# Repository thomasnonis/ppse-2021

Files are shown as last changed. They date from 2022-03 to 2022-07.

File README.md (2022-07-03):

# Abstract
This is the repository for SALMO, the Solar Azimuth and eLevation Motorized lOcator. It is a PCB used for driving a tracking solar panel system, using GPS location and a MPPT algorithm to maximise the incident power.  
The official name of the project is `PPS2021_SUN_TRK`

# About the project
During the second semester of the 2021/2022 A.Y. of their bachelor degree in Electronics Engineering, a group of students known as _SALMO SOCIETY_, developed a custom board to solve real world problems. 
<br>Nowadays, we are all aware about climate change and it's impact, so the _SALMO SOCIETY_ decided in partecipate to the renewable energy run, in particular exploiting the energy obtained by a solar panel to drive a load.
<br>The aim of the board it's to move the solar panel using two step motors (along z-y axis) facilitating the MPP (Maximum Power Point) reaching and, as consequence, delivering the maximum power to the load.<br> Using a GPS module, the board knows exactly where it is located around the globe; afterwards the position of the sun is computed with a specific algorithm based on astronomical calculations. Then, the spatial position of the panel is derived by the accelerometer and compass modules; lastly, the motor is moved in order to follow the exact position of the sun (given its azimuth and elevation).

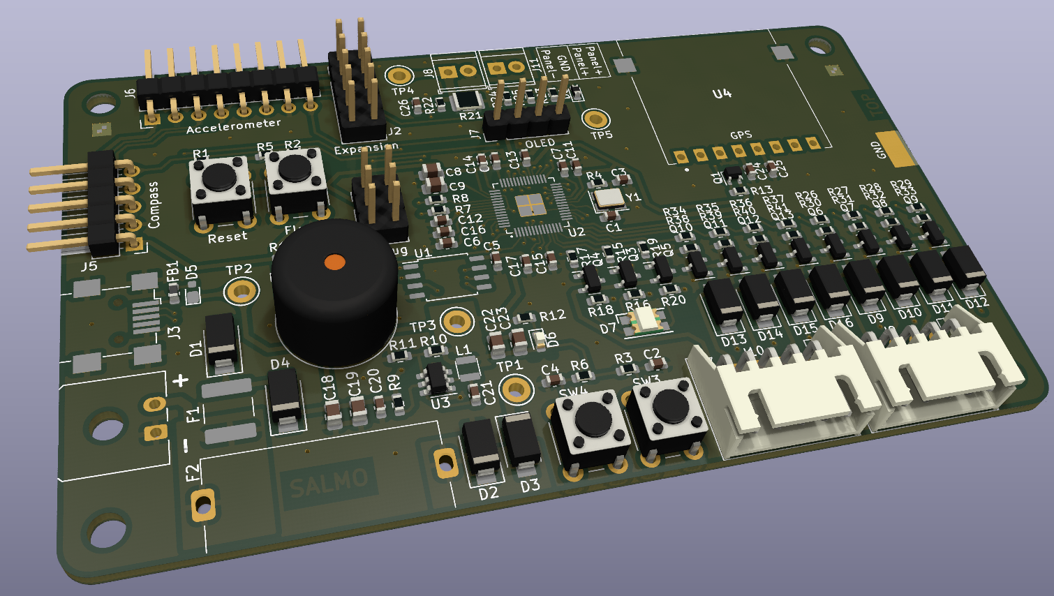
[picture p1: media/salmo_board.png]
Salmo board


# Repo structure

    📂 SALMO_pico_fw    -> Firmware 
    📂 datasheets       -> Datasheet of every component mounted on board
    📂 kicad-project    -> KiCad and gerber files 
    
# :rainbow: Building process

Debian:

    sudo apt install cmake gcc-arm-none-eabi libnewlib-arm-none-eabi build-essential

Fedora:

    sudo dnf install cmake
    sudo dnf group install "C Development Tools and Libraries" "Development Tools"
    sudo dnf install gcc-arm-linux-gnu \
    arm-none-eabi-gcc-cs-c++ \
    arm-none-eabi-gcc-cs \
    arm-none-eabi-binutils \
    arm-none-eabi-newlib

then:

    git pull
    git submodule update --init --recursive

now add to your shell profile (`~/.bashrc` or `~/.zshrc`) the current directory (pico-sdk folder) as env variable:
 
`export PICO_SDK_PATH=<path_to>/pico-sdk`

Windows:

Follow this [guide](https://shawnhymel.com/2096/how-to-set-up-raspberry-pi-pico-c-c-toolchain-on-windows-with-vs-code/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) and you're good to go.

Finally, in order to compile:

    cd SALMO_pico_fw
    mkdir build
    cd build 
    cmake ..
    cd src
    make -j4

After this process some binaries files will be created. <br>The suitable one is the `.uf2` file, which is located into `SALMO_pico_fw/build/src`.<br>
Now you can start the board in bootloader mode:
1. Disconnect the board
1. Hold the `BOOTSEL` button
1. Connect the device to your computer

Then drag and drop the `.uf2` file to `RPI-RP2` mass storage device.

## Picotool
If you want to install picotool and easily flash when RP2040 is not in BOOTSEL mode, you need to follow these steps:

### Debian:

    sudo apt install build-essential pkg-config libusb-1.0-0-dev

### Fedora:

    sudo dnf install libusb-devel libusb libusb1-devel systemd-devel
    sudo reboot

### Mac:

    xcode-select --install
    brew install libusb
    brew link --overwrite libusb
    
### Windows:    
For now Picotool doesn't seem to work on Windows, skip these steps and flash "manually" moving the `.uf2` file.

### Compiling Picotool
After you have downloaded picotool you have to compile it:

    cd picotool
    mkdir build
    cd build
    cmake ..
    make

Afterwards, you must give execution permissions to the scripts:

    cd ../../SALMO_pico_fw/src
    sudo chmod +x build.sh
    sudo chmod +x flash.sh
    sudo chmod +x build_and_flash.sh

If something on MacOS doesn't work use

    sudo chown -R {username}:{workgroup} ppse-2021

Then, you can simply navigate to `SALMO_pico_fw/src/` and execute `build.sh`, `flash.sh` or `build_and_flash.sh` to respectively build, flash or build and flash the project. :nail_care:

# Firmware flow chart
```mermaid
graph TB
A[Peripherals initialization] -->B(Infinite loop)
    B --> C{Is go home btn pressed?}
    C -->|Yes| D(Go home) --> E
    C -->|No| E{Is tracking enable btn pressed?}
	E -->|Yes| E1(Enable or disable tracking mode) --> F
	F{Is update_motor_position_timer elapsed <br>and tracking mode on?}
	F -->|Yes| G(Update motor position) --> H
	F -->|No| H{Is gps timer elapsed?}
	E -->|No| H
	H -->|Yes| I(Read and parse GPS output) --> L
	H -->|No| L{Is update sun position timer elapsed?}
	L -->|Yes| M(Run algorithm to compute sun position based on GPS data) --> B
	L -->|No| B
```

# How to contribute to the project
In this sections you can find some guidelines in order in order to contribute with out project

## Commits

A good commit message should be preceded by a prefix, then a colon and then a brief and descriptive comment on the changes made.  
All commits should be written in the present simple tense (eg. add file, modify this, edit that).  
Commits may also include longer descriptions in the second argument of a commit message.

Following are the prefix conventions for this repository.

- `hw:` for hardware (schematic, pcb, ...)
- `fw:` for firmware
- `sw:` for software (interfaces on a pc and such)
- `docs:` for documentation
- `notes:` for lecture notes
- `chore:` for general tasks (file management, moving stuff around, ...)

:x: `git commit -m "Added some features to code"`  
:heavy_check_mark: `git commit -m "fw: add uart implementation to gps driver"`

## File naming

All files must have no spaces and should be lowercase.

:x: Name of file.ext  
:heavy_check_mark: name-of-file.ext 

## :briefcase: Adding new drivers or libraries
If you want to add a new driver or library please keep this tree structure
```
📦 SALMO_pico_fw
 ┣📜 CMakeLists.txt (Project cmake file)
 ┣ 📂 build
 ┣ 📂 src
 ┗ 📜 CMakeLists.txt (SALMO.C cmake file)
 ┣ 📂 your_lib
 ┃ ┗ 📂 your_lib docs
 ┃ ┗ 📜 CMakeLists.txt (lib cmake file)
 ┃ ┗ 📜 your_lib.c.
 ┃ ┗ 📜 your_lib.h
```
Every library needs some sort of documentation, and of course a cmake file!

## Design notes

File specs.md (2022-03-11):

# Packages

## Crystal

- 3225

## Resistors

- Standard: 0603
- Mid power: 0805
- Shunts: 1210

## Capacitors

- 100n: 0603
- 1u: 0603
- \>10u: 0805 (_In order to distinguish them from the smaller ones_)

## Flash

- SO8

## USB

- Either B or micro B

# To research

- RMII (Ethernet)
- Search where to buy the RT6150B Buck Boost on the Rpi Pico

Modello non disponibile da nessuna parte. Esempi di alternative su farnell:

[Farnell](https://it.farnell.com/w/c/semiconduttori-circuiti-integrati/circuiti-integrati-di-gestione-di-potenza-pmic/regolatori-di-tensione/regolatori-switching-fissi-dc-dc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|3.3v&tensione-di-ingresso-max=36v|45v&tensione-di-uscita-nom-=3.3v&range=inc-in-stock)

| Device | In range | Out range | Out current | URL |
|---|---|---|---|---|
| MPQ4313 | 3.3 - 45 | 3.3V, 5V fixed | 3A | [datasheet](https://www.farnell.com/datasheets/3183543.pdf) | 
| MAX2040x | 3.0 - 36 | 0.8 - 10 | 4-8A | [datasheet](https://www.farnell.com/datasheets/3497518.pdf) | 
| MAX20004/6/8 | 3.0 - 36 | 1 - 5 | 4/6/8A | [datasheet](https://www.farnell.com/datasheets/3108373.pdf) | 
| MPQ9840 | 3.3 - 36 | ? | 3.5A | [datasheet](https://www.farnell.com/datasheets/3380075.pdf) | 

# Peripherals

- GPS
  -  SAM8Q (SMD) or PAM7Q (THT)
  -  Connect UART as predisposition
  -  Extend pads for manual soldering
  -  Supply control with pMOS and PDTC114YT. No direct drive to MOSFET, since there could be a current throught the internal protection diode of the GPIO

- RGB LED

# Power

- USB 5V
- 3.3V Battery
- 24V input

- MP2322 Buck concverter from supply to 3V3 (just as exercise, it does not support 24V)
- JST 2.5 01x02 for battery
- Screw connector for 24V (5,04)

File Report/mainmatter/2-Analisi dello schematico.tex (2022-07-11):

\chapter{Analisi dello schematico}

I principali componenti utilizzati per la realizzazione del progetto
sono:

\begin{itemize}
\item
  
  microcontrollore \emph{RP2040};
  
\item
  
  memoria flash \emph{QSPI} \emph{W25Q16JV};
  
\item
  
  regolatore di tensione \emph{TPS563201};
  
\item
  
  \emph{GPS PAM7Q};
  
\item
  
  magnetometro \emph{HMC5883L};
  
\item
  
  accelerometro e giroscopio \emph{MPU6050};
  
\item
  
  2 motori stepper unipolari con riduttore \emph{28BYJ (ADAFRUIT 918)};
  
\item
  
  circuiti di misura tensione e corrente;
  
\item
  
  display \emph{OLED} 128x64;
  
\item
  
  USB type B-mini;
  
\item
  
  buzzer;
  
\item
  
  led \emph{RGB 1210}.
  
\end{itemize}

\noindent Per una maggior chiarezza abbiamo deciso di dividere lo schematico in
più fogli, ognuno con una funzione ben precisa:

\begin{itemize}
\item
  
  \textbf{Control}: \emph{MCU}, \emph{Flash}, Oscillatore al quarzo,
  pulsanti ecc..
  
\item
  
  \textbf{Power}: Regolatore di tensione, \emph{USB}
  
\item
  
  \textbf{Peripherals}: GPS, Magnetometro, Accelerometro, \emph{OLED},
  Buzzer, Led \emph{RGB}
  
\item
  
  \textbf{Panel} \textbf{sensing}: Current sensing, Voltage Sensing
  
\item
  
  \textbf{Actuation}: Stepper Driver
  
\end{itemize}

\begin{center}

\captionsetup{type=figure}
\captionof{figure}{Foglio "Main" SALMO}
\end{center}

\hypertarget{control}{%
\section{Control}\label{control}}

Il foglio ``\emph{Control}'' include i componenti adibiti al controllo
della scheda, quali:

\begin{itemize}
\item
  
  microcontrollore \emph{RP2040};
  
\item
  
  memoria flash SPI \emph{W25Q16JV};
  
\item
  
  cristallo al quarzo a 12 \emph{MHz};
  
\item
  
  pulsanti di reset, boot, home e tracking enable;
  
\item
  
  connettori di debug ed espansione.
  
\end{itemize}

\begin{center}
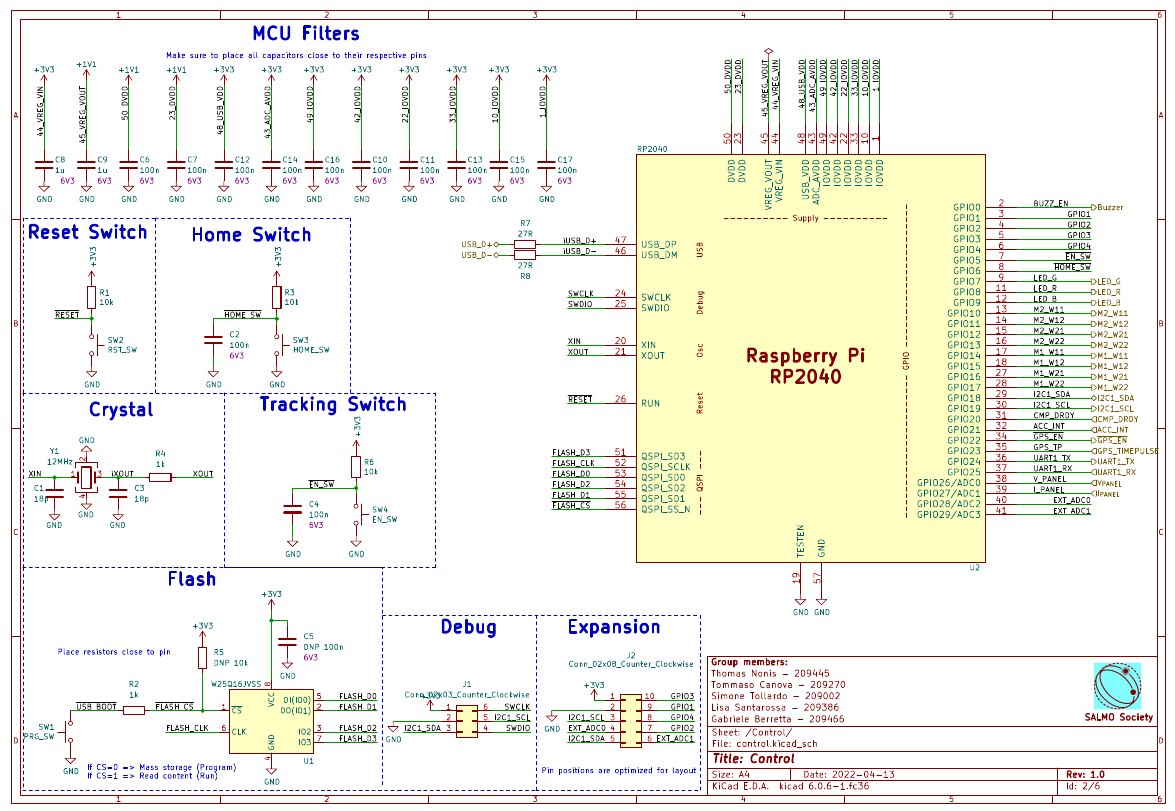
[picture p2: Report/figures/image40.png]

\captionsetup{type=figure}
\captionof{figure}{Foglio "Control" SALMO}
\end{center}

\hypertarget{microcontrollore-rp-2040}{%
\subsection{\texorpdfstring{Microcontrollore: RP
2040}{ Microcontrollore: RP 2040}}\label{microcontrollore-rp-2040}}

La scheda si avvale dell'ormai celeberrimo \emph{MCU} di Raspberry Pi Ltd: \emph{RP2040}.\\
Caratteristiche principali:

\begin{itemize}
\item
  
  133 \emph{MHz} dual core 32 bit ARM Cortex-M0+;
  
\item
  
  264 \emph{KB} SRAM;
  
\item
  
  Nessuna memoria flash interna;
  
\item
  
  Controller bus \emph{QSPI}, che supporta fino a 16 MB di memoria flash
  esterna;
  
\item
  
  Controllore \emph{DMA};
  
\item
  
  Crossbar \emph{AHB} (Advanced High-performance Bus);
  
\item
  
  Regolatore \emph{LDO} programmabile per generare la tensione del core
  integrato;
  
\item
  
  2 \emph{PLL} su chip per generare clock USB e core;
  
\item
  
  30 pin \emph{GPIO}, di cui 4 utilizzabili opzionalmente come ingressi
  analogici.
  
\end{itemize}

\noindent Periferiche:

\begin{itemize}
\item
  
  2 \emph{UART};
  
\item
  
  2 controller \emph{SPI};
  
\item
  
  2 controller \emph{I²C};
  
\item
  
  16 canali \emph{PWM};
  
\item
  
  Controller USB 1.1 e \emph{PHY}, con supporto per host e dispositivo;
  
\item
  
  8 macchine a stati di input-output (\emph{PIO}) programmabili.
  
\end{itemize}

\noindent Il microcontrollore, oltre ad eseguire l'algoritmo di calcolo della 
posizione della nostra stella, ha il compito di gestire le periferiche, in
particolare:

\begin{itemize}
\item
  
  genera il segnale di rotazione dei motori quando previsto
  dall'algoritmo implementato (\emph{GPIO} da 10 a 17);
  
\item
  
  comunica con il GPS tramite interfaccia UART (\emph{GPIO} 24 e 25);
  
\item
  
  comunica con il magnetometro, con l'accelerometro e con il display
  OLED mediante interfaccia I2C (\emph{GPIO} 18 \emph{SDA}, \emph{GPIO}
  19 \emph{SCL});
  
\item
  
  effettua le misure di corrente e di tensione del pannello (\emph{GPIO}
  26 e 27);
  
\item
  
  gestisce il buzzer (\emph{GPIO} 0) ed un led \emph{RGB} (\emph{GPIO}
  7, 8, 9);
  
\item
  
  comunica con la memoria \emph{flash} (pin da 51 a 56);
  
\item
  
  gestisce l'interfaccia \emph{USB} (pin 46 e 47).
  
\end{itemize}

\begin{center}
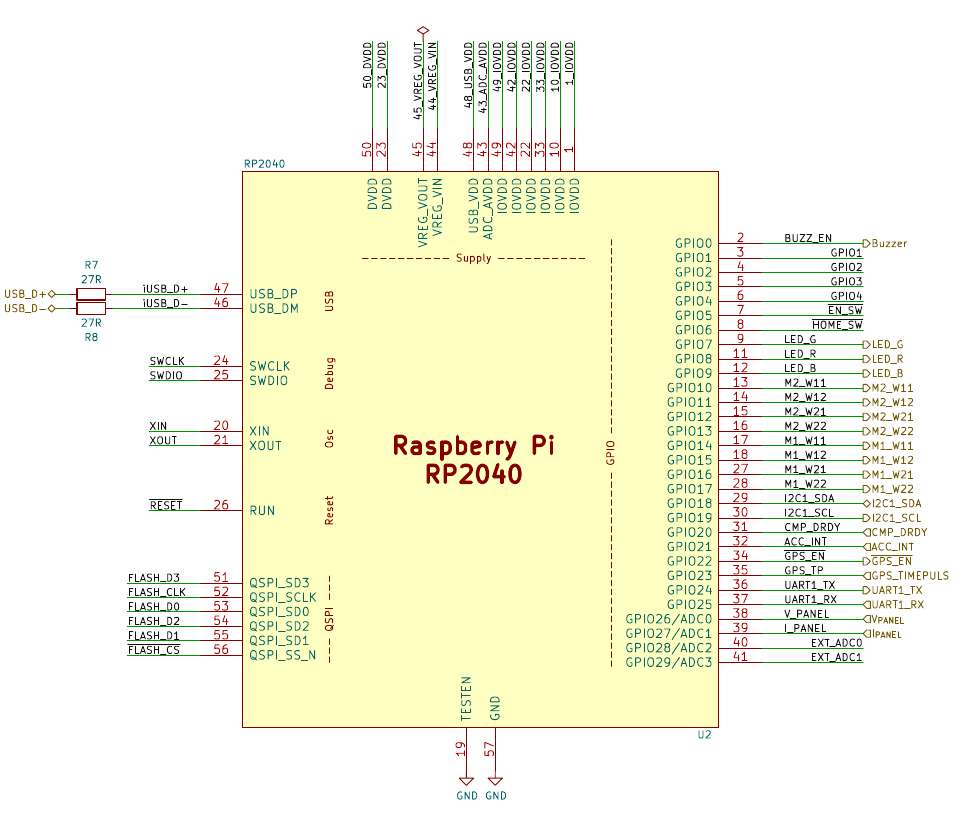
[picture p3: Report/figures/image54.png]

\captionsetup{type=figure}
\captionof{figure}{Schema pin microcontrollore RP2040}
\end{center}

\noindent Per ridurre il rumore ad alta frequenza presente sulla linea di
alimentazione abbiamo previsto dei condensatori di filtro per
cortocircuitare a massa la componente alternata (andranno poi
posizionati il più vicino possibile ai pin del MCU).

\begin{center}
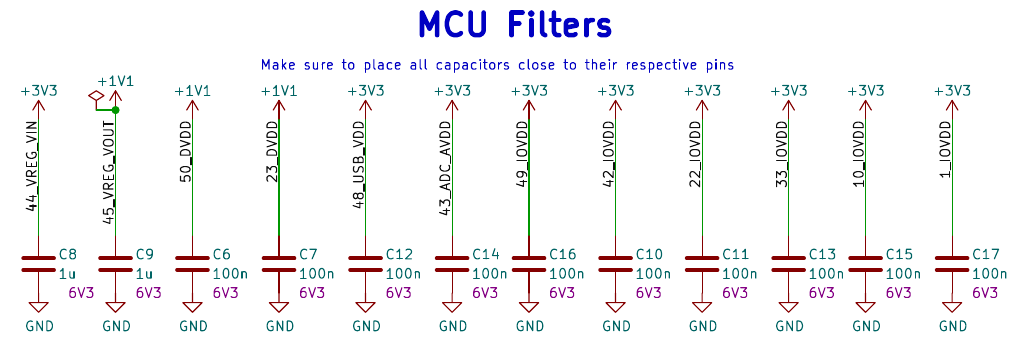
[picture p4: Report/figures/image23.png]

\captionsetup{type=figure}
\captionof{figure}{Condensatori di bypass MCU}
\end{center}

\hypertarget{pulsanti}{%
\subsection{\texorpdfstring{Pulsanti}{ Pulsanti}}\label{pulsanti}}

Per il progetto \emph{SALMO} abbiamo previsto quattro pulsanti tattili:

\begin{itemize}
\item
  
  Un pulsante di reset (\emph{SW2}) per poter resettare il
  microcontrollore;
  
\item
  
  Un pulsante per portare il microcontrollore in modalità
  \emph{bootloader (SW1)}, in modo tale da poter "flashare" il
  programma via USB.
  
\item
  
  Un pulsante (\emph{SW3}), denominato "Home", che permette di portare
  il sistema di puntamento del pannello solare ad una posizione
  predefinita (0° Nord, 45° Elevazione);
  
\item
  
  Un pulsante (\emph{SW4}), denominato "Tracking Enable", che permette
  di far partire il sistema di puntamento del pannello;
  
\end{itemize}

\begin{center}
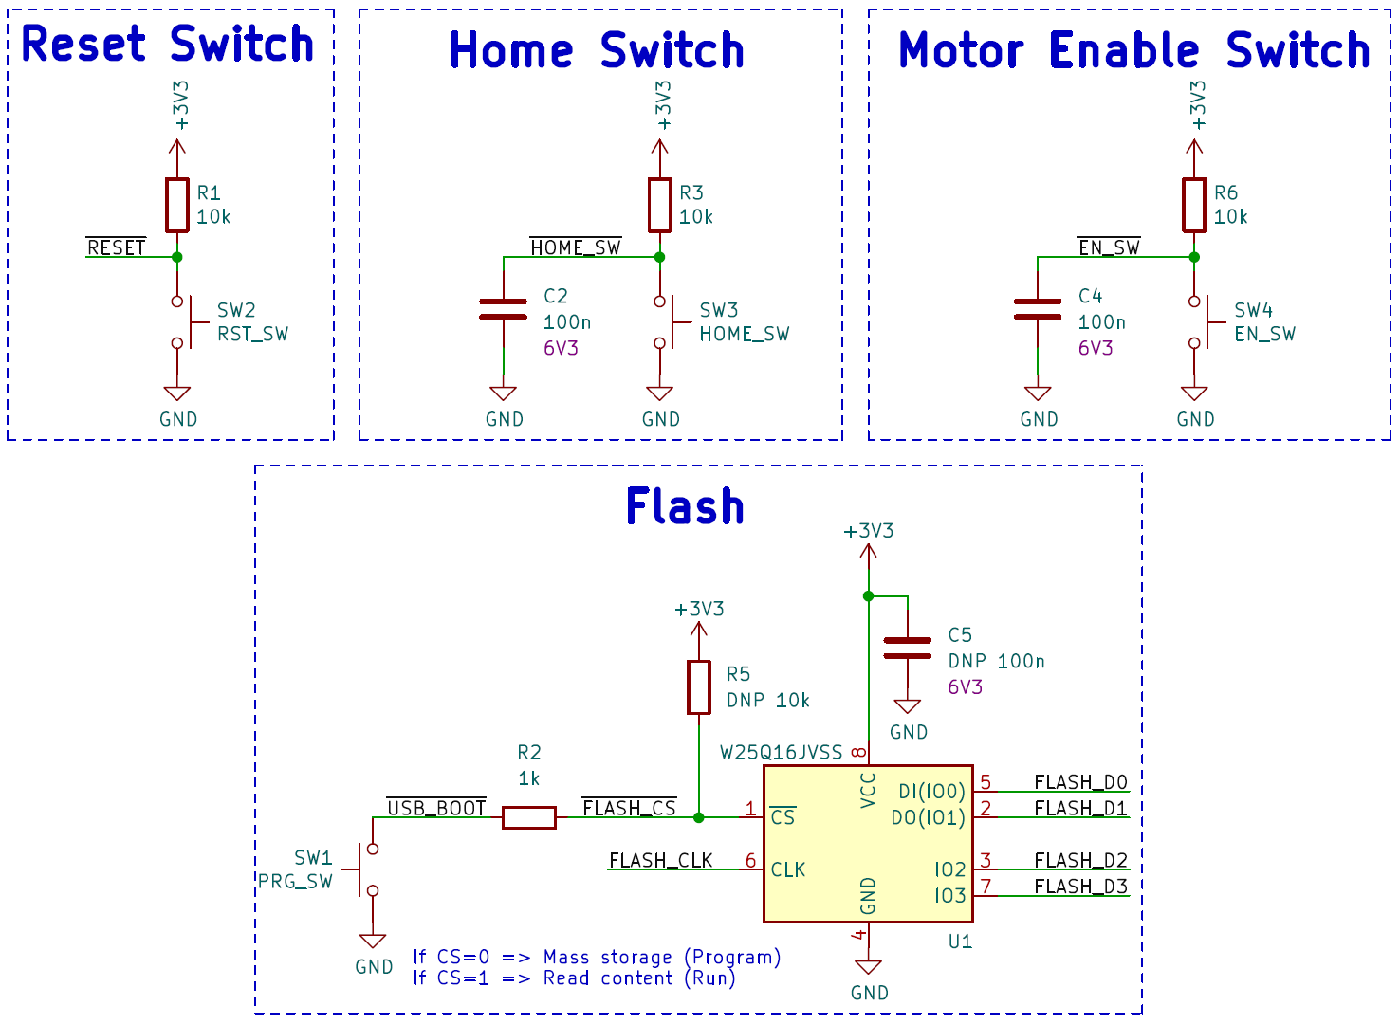
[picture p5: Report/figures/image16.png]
  
  \captionsetup{type=figure}
  \captionof{figure}{Pulsanti SALMO}
\end{center}

\noindent Per ogni pulsante abbiamo previsto un resistore di pull-up da 10kΩ, che
nel caso del pulsante di programmazione è contrassegnato come \emph{DNP}
(Do Not Place), poiché la memoria fornisce un \emph{pull-up} interno che
lo rende non necessario.\\
Per i pulsanti di \emph{reset} e programmazione non abbiamo previsto
alcun filtro di debouncing come consigliato dai relativi datasheet,
mentre per i restanti abbiamo aggiunto un condensatore da \emph{100nF}
per introdurre una costante di tempo di \emph{1ms}.\\
La resistenza \emph{R2} in serie al pulsante di programmazione è stata inserita
seguendo i consigli del manuale di sviluppo hardware del RP2040
(probabilmente il pin $\overline{\rm {CS}}$ della flash non ha una
resistenza di limitazione interna).\\
I pulsanti scelti sono dei generici \emph{tactile switch} da 6mm a
tecnologia TH.

\hypertarget{quarzo}{%
\subsection{Quarzo}\label{quarzo}}

Per generare il segnale di clock del microcontrollore abbiamo
selezionato un quarzo da 12 \emph{MHz}. In particolare abbiamo
utilizzato un quarzo a 4 pin con package \emph{3225}, essendo questo uno
dei constraint imposti dal professore ad inizio progetto. Per il
dimensionamento del resistore in serie e dei condensatori abbiamo
seguito le linee guida del manuale di sviluppo hardware del RP2040.\\
\(C_{1} = C_{2} = 2 \cdot (C_{L} - C_{\text{Parassita}})\)
, dove \(C_{L}\) è la capacità di load ottimale del quarzo.\\
Ipotizzando quindi una capacità parassita pari a 5pF ed una capacità di
load di 14pF otteniamo \(C_{1} = C_{2} =18pF\).

\begin{center}
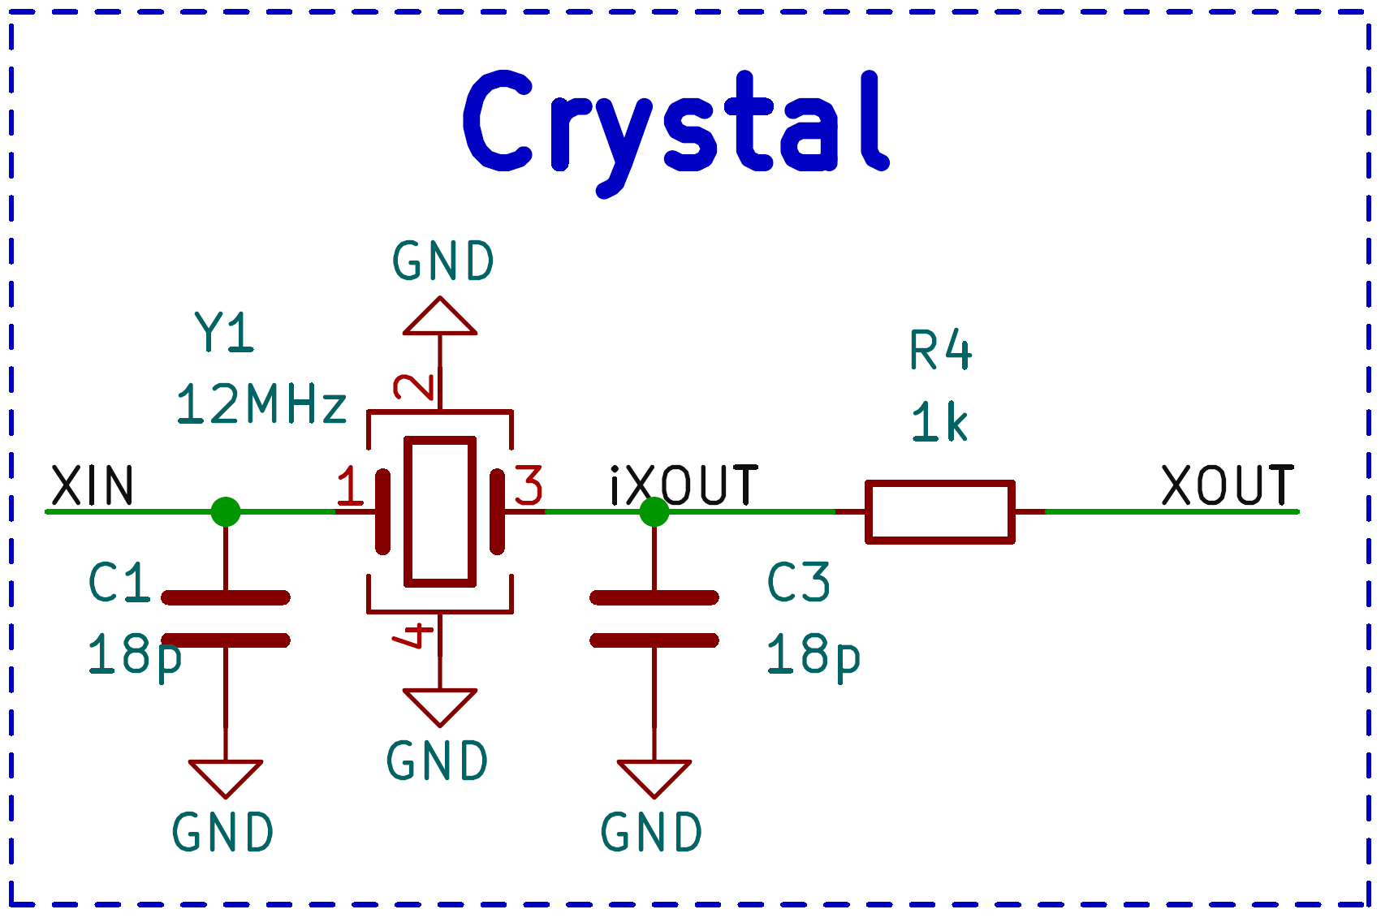
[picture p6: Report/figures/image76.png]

\captionsetup{type=figure}
\captionof{figure}{Circuito del cristallo di quarzo di SALMO}
\end{center}

\noindent La capacità di carico è particolarmente importante perché, essendo la
capacità totale vista dai due pin del cristallo \emph{XIN} e \emph{XOUT}, può portare
il cristallo ad oscillare in un punto specifico tra la sua frequenza
minima e massima. Cambiando la capacità del carico si otterrà quindi una
diversa frequenza di oscillazione. Ecco perché il produttore di
cristalli fornisce la frequenza del cristallo a una capacità di carico
specifica, che in questo caso è di 14pF.

\begin{center}
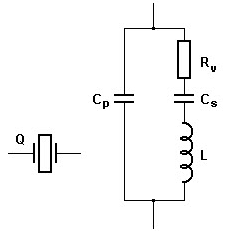
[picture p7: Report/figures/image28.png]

\captionsetup{type=figure}
\captionof{figure}{Modello RLC di un cristallo al quarzo in risonanza parallelo}
\end{center}

\hypertarget{memoria-flash}{%
\subsection{\texorpdfstring{Memoria flash}{ Memoria flash}}\label{memoria-flash}}

Essendo il microcontrollore sprovvisto di una memoria flash interna, 
è necessario installarne una esterna in cui poter salvare il firmware compilato in formato
binario \emph{.uf2}, il quale all'accensione verrà eseguito dal bootloader. La
memoria flash utilizzata è la \emph{W25Q16JV}, caratterizzata da una capacità di 16MB e dall’interfaccia di comunicazione \emph{Quad-SPI}.
Il protocollo \emph{QSPI} è particolarmente diffuso nel ramo delle comunicazioni con memorie flash,
come nel caso presente sulla scheda. Rispetto allo standard \emph{SPI}, sono
presenti 4 linee di dato bidirezionali, rispettivamente \emph{I0, I1,
I2, I3} (che vanno dunque a sostituire \emph{MISO} e \emph{MOSI}), che
permettono un trasferimento dati dalle 4 alle 6 volte più veloce
rispetto ad una normale interfaccia \emph{SPI}.

\begin{center}
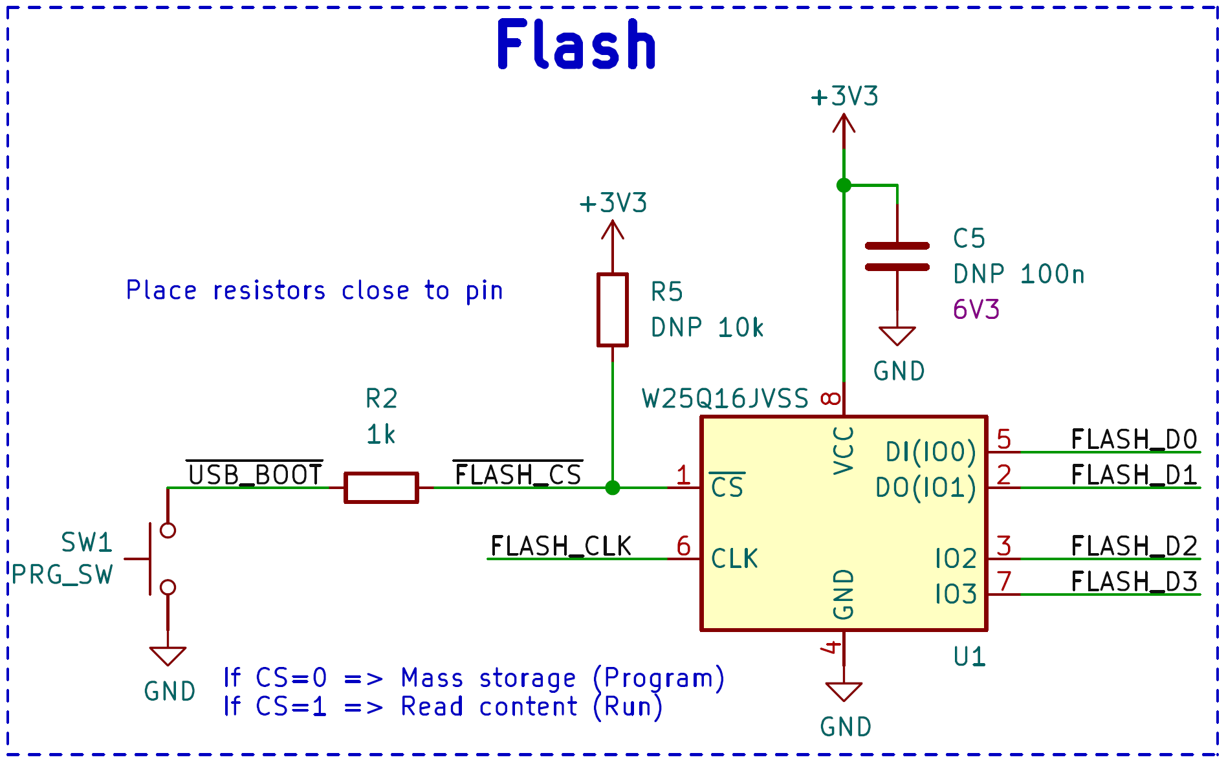
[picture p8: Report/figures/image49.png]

\captionsetup{type=figure}
\captionof{figure}{Circuito flash SALMO}
\end{center}

\noindent Il pin $\overline{\rm {CS}}$ permette di abilitare o
disabilitare la comunicazione \emph{QSPI}, quando $\overline{\rm {CS}}$=1 i pin di
comunicazione rimangono ad alta impedenza, mentre quando $\overline{\rm {CS}}$=0 è
possibile interfacciarsi con la memoria per salvare il programma.
Sul pin di alimentazione è presente un condensatore di decoupling da 100nF per filtrare rumore ad alta
frequenza sulla linea di alimentazione.

\hypertarget{debug-ed-espansione}{%
\subsection{\texorpdfstring{Debug ed espansione}{ Debug ed espansione}}\label{debug-ed-espansione}}

\begin{center}
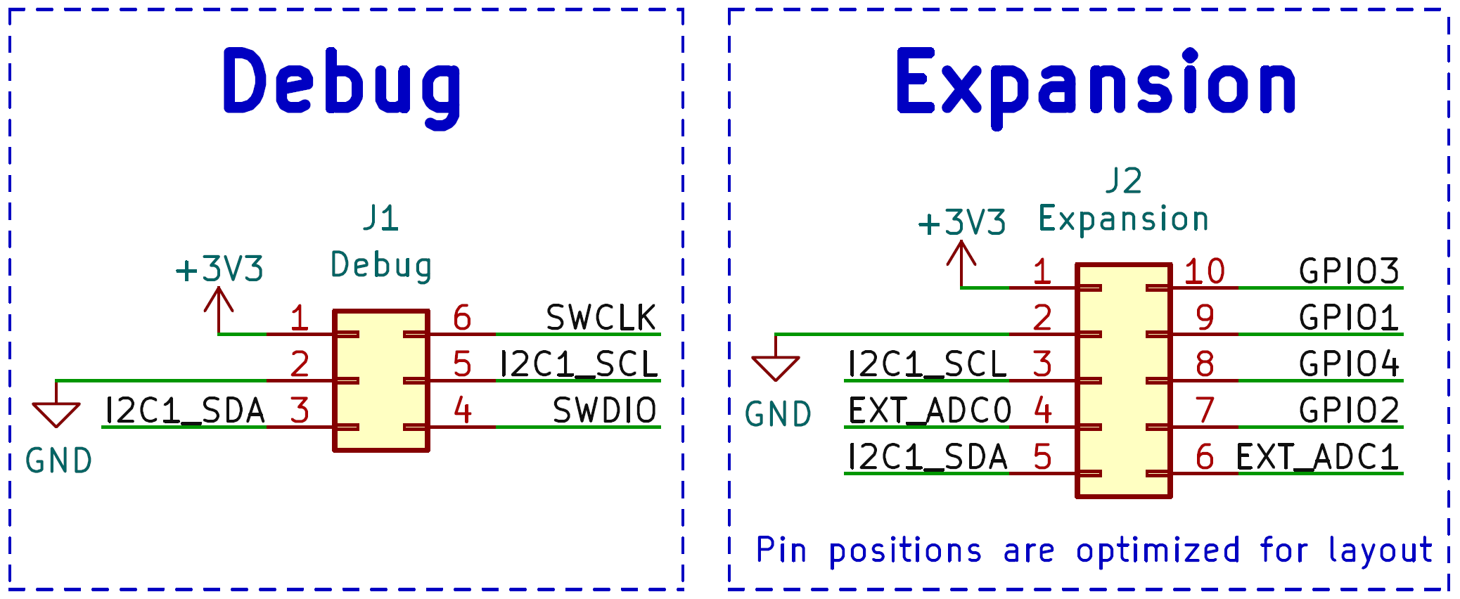
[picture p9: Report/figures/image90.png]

\captionsetup{type=figure}
\captionof{figure}{Connettori Debug ed Expansion SALMO}
\end{center}

\noindent Per permettere al microcontrollore di comunicare con eventuali unità
esterne, sulla scheda abbiamo inserito un connettore a 10 pin con le
linee \emph{$I^2C$}, i due canali non utilizzati del convertitore analogico
digitale ed i rimanenti \emph{GPIO} non utilizzati.\\
Abbiamo previsto anche un connettore per il debug con interfaccia SWD
(\emph{Serial Wire Debug}), alimentazione per il microcontrollore e bus
\emph{I2C}. Per il debug è possibile persino utilizzare un altro \emph{RP2040}.\\
È sufficiente collegare le linee di \emph{SWData} e
\emph{SWClock} e l'alimentazione necessaria al debugger,
dopodichè si può flashare quest'ultimo con \emph{picoprobe.uf2}
(programma situato nella cartella degli esempi offerti per \emph{RP2040},
vedasi capitolo
\protect\hyperlink{_w8kvxnysumpc}{\underline{Firmware}}), per poi
interfacciarsi via usb utilizzando \emph{GDB} ed \emph{OpenOCD}.

\begin{center}
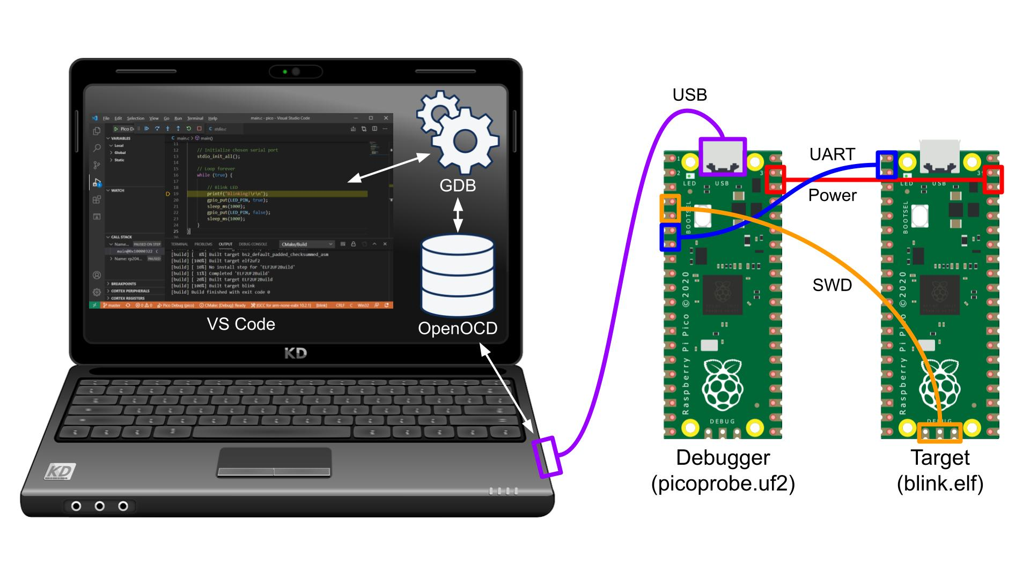
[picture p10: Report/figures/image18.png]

\captionsetup{type=figure}
\captionof{figure}{Immagine illustrativa del debug di un Pi Pico mediante un altro Pi Pico}
\end{center}

\hypertarget{power}{%
\section{Power}\label{power}}

\begin{center}
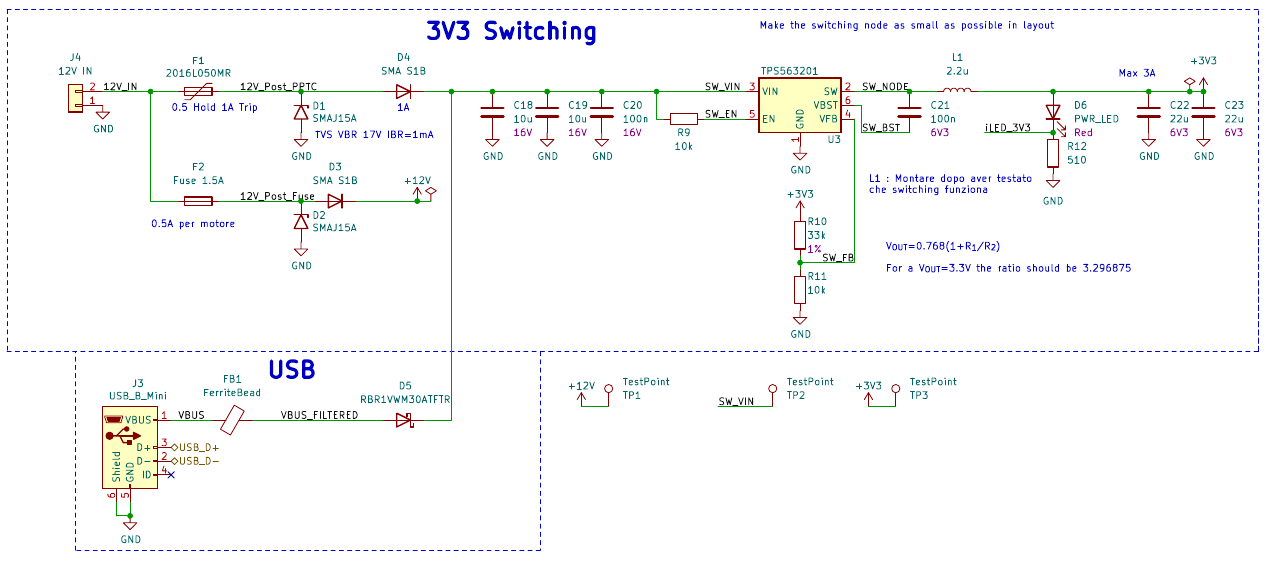
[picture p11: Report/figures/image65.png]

\captionsetup{type=figure}
\captionof{figure}{Foglio "Power" SALMO}
\end{center}

\noindent Per il funzionamento della scheda sono necessari due livelli di tensione: 
12V per il controllo dei motori e per il led RGB e 3.3V per i restanti componenti. 
I 12V provengono direttamente da un alimentatore esterno (collegato al connettore J4), 
mentre i 3.3V vengono ottenuti da un convertitore switching di tipo buck (step-down). 
È inoltre prevista la possibilità di alimentare la logica di controllo tramite un connettore USB (J3). 
Suddividiamo quindi il circuito di alimentazione in tre macro-blocchi: input 5V, input 12V e regolatore di tensione.

\hypertarget{input-5V}{
\subsection{\texorpdfstring{Input 5V}{Input 5V}}\label{input-5V}}

Per permettere di alimentare la scheda anche senza la necessità di collegare un 
alimentatore da 12V, principalmente per il debug e lo sviluppo firmware, abbiamo 
previsto un connettore USB di tipo B-mini (il pin ID è stato lasciato flottante non 
dovendo utilizzare la funzione USB OTG, fissando il dispositivo come device).\\
Questo fornisce una tensione di 5V in ingresso al regolatore switching, che permette di generare i 3.3V 
necessari alla scheda. Per evitare che i 12V possano propagarsi sulla rail di alimentazione dell’USB abbiamo 
aggiunto in serie un diodo (D5) di tipo \emph{Schottky}, così da avere perdite minori grazie alla caduta di tensione 
caratteristica di soli 0,33V.
Abbiamo inoltre aggiunto una \emph{ferrite bead}, caratterizzata da una resistenza di 120Ω a 100MHz, per
ridurre il rumore ad alta frequenza.

\begin{center}
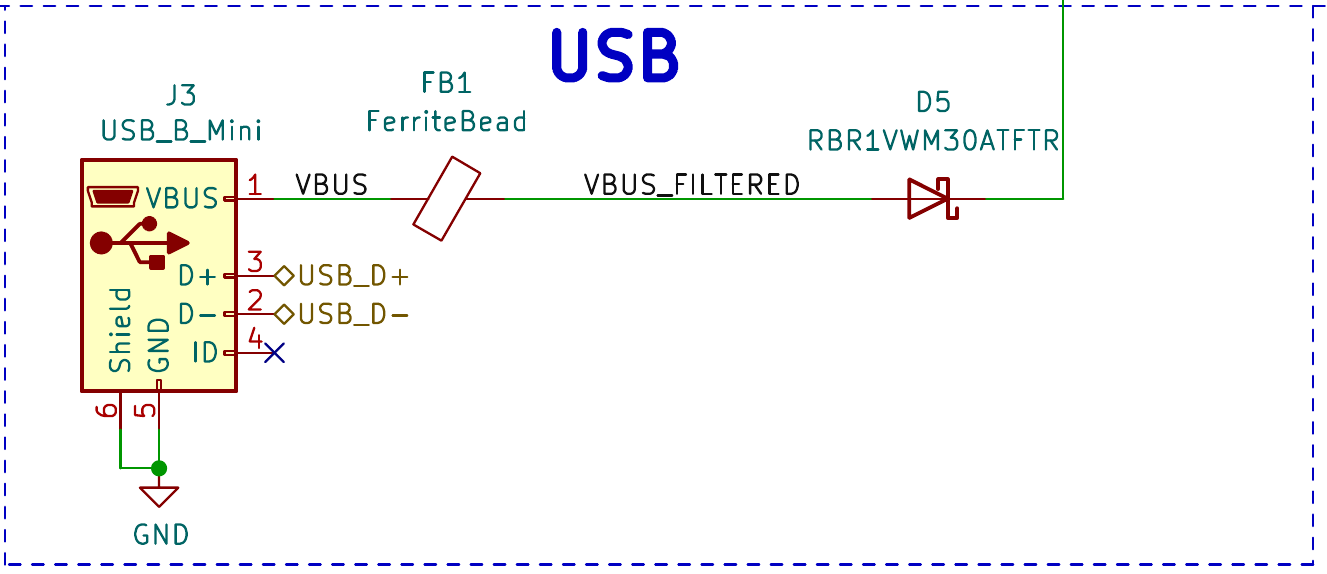
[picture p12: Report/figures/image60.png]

\captionsetup{type=figure}
\captionof{figure}{Alimentazione via USB}
\end{center}

\hypertarget{input-12V}{%
\subsection{\texorpdfstring{Input 12V}{Input 12V}}\label{input-12V}}

Per il regime di funzionamento normale l’alimentazione proviene dal connettore J4 ad una tensione nominale di 12V. 
Questo fornisce alimentazione sia ai motori e al led RGB, che al convertitore switching, tramite due rami separati.
Per l’alimentazione “di potenza” abbiamo previsto un circuito di protezione composto da un fusibile per protezione da sovracorrenti, 
un diodo TVS per protezione da sovratensioni transitorie ed un diodo rettificatore per bloccare correnti inverse. La corrente massima assorbita da 
ciascun motore è di circa 0.5A, perciò abbiamo scelto un fusibile da 1.5A (tenendo conto di qualche centinaio di mA per il led RGB 
e qualche altro per avere una minima tolleranza).\\
Il TVS invece è uno \emph{SMAJ15A}, in grado di dissipare 400W per transitori di durata fino a 10us, mentre il diodo in serie è un \textit{SMA S1B}
(D4), un rettificatore generico.\\
Il ramo che riguarda l’alimentazione del convertitore switching è protetto in modo simile, con la sola differenza che la protezione 
dalle sovracorrenti avviene tramite un fusibile resettabile, o \textit{PPTC} (Polymeric Positive Temperature Coefficient).

\begin{center}
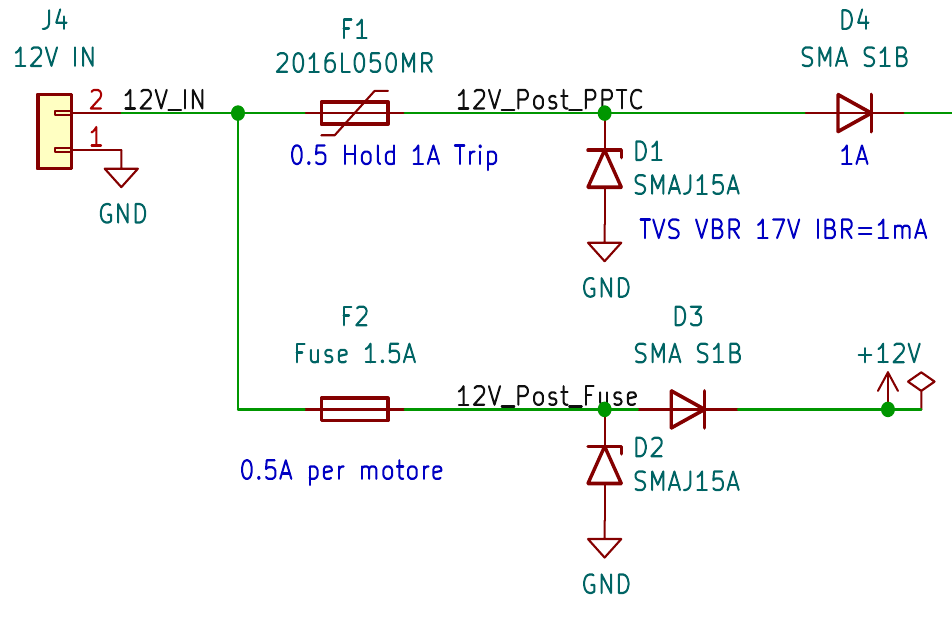
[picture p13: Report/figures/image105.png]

\captionsetup{type=figure}
\captionof{figure}{Rami 12V e regolatore di tensione}
\end{center}

\hypertarget{regolatore-di-tensione}{%
\subsection{\texorpdfstring{Regolatore di tensione}{Regolatore di tensione}}\label{regolatore-di-tensione}}

I diodi D4 e D5 svolgono la funzione equivalente di OR logico per garantire in ogni caso l’alimentazione al regolatore switching,
un \emph{TPS563201}, con tensione in ingresso minima di 4.5V e massima di 17V.\\
Per avere in output una tensione di 3.3V, il pin di feedback VFB del regolatore deve essere connesso, tramite un partitore, alla linea di uscita.\\
Il rapporto di partizione è dettato dalla seguente formula:\\
\[V_{out} = 0.768(1 + \frac{R10}{R11})\]
per cui ne consegue che per avere $V_{out}=3.3V$ dobbiamo avere:\\
\[\frac{R10}{R11} = \ 3.3\]

Al fine di segnalare la presenza dei 3.3V, abbiamo previsto un led rosso con $V_F=2V$.
Imponendo quindi una corrente di 2.5mA abbiamo scelto una resistenza in serie al diodo da 510 Ω.

\begin{center}
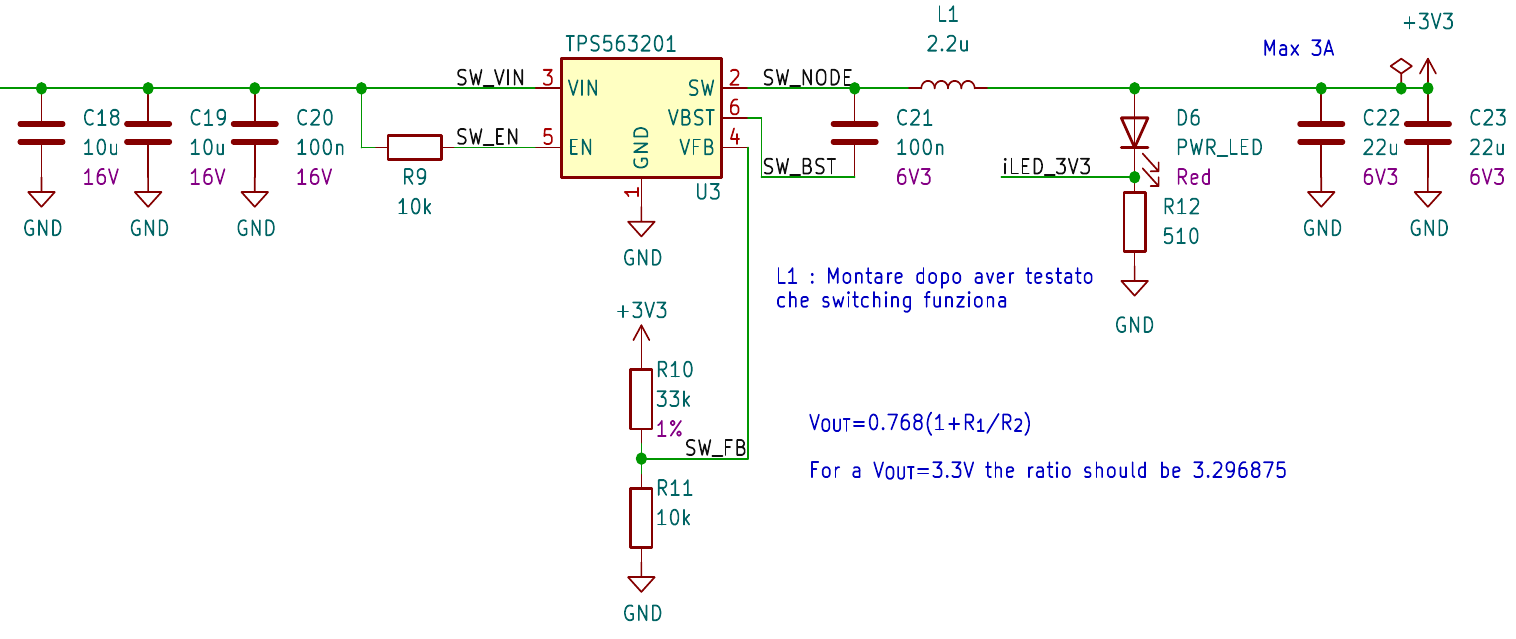
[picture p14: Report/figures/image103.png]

\captionsetup{type=figure}
\captionof{figure}{Circuito regolatore di tensione buck}
\end{center}
      
\noindent Per il dimensionamento dei filtri di ingresso e uscita ci siamo affidati alle \textit{design guidelines} del datasheet del dispositivo. Sul ramo di ingresso abbiamo quindi posto in parallelo tre condensatori (due da 10u e uno da 100n), mentre su quello di uscita abbiamo inserito in serie un’induttanza da 2.2uH ed in parallelo due condensatori da 22u. Il fatto di utilizzare più condensatori in parallelo si giustifica considerando il loro modello equivalente reale. Si osserva infatti che la resistenza e l’induttanza parassita di condensatori in parallelo diminuisce, dando luogo ad una capacità con caratteristiche migliori rispetto ad un singolo condensatore di capacità pari alla loro somma.

\begin{center}
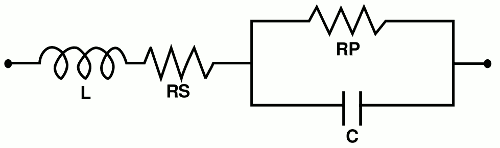
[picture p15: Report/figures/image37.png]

\captionsetup{type=figure}
\captionof{figure}{Modello RLC di un condensatore reale}
\end{center}

\noindent Sempre seguendo le linee guida del costruttore, prima dell’induttore, 
quindi sul nodo di commutazione, abbiamo inserito un condensatore da 100n collegato al pin di \textit{bootstrap}.
Il regolatore prevede inoltre un pin di abilitazione che abbiamo deciso di collegare permanentemente, 
tramite un resistore da 10k, alla linea di ingresso, cosicché la scheda venga alimentata non appena ci 
sia una tensione adeguata in ingresso.\\
Abbiamo infine previsto dei test point per il controllo delle varie
tensioni sul pannello in fase di debug.

\begin{center}

\captionsetup{type=figure}
\captionof{figure}{Testpoint per la misura delle tensioni di alimentazione}
\end{center}

\hypertarget{peripherals}{%
\section{Peripherals}\label{peripherals}}

\begin{center}
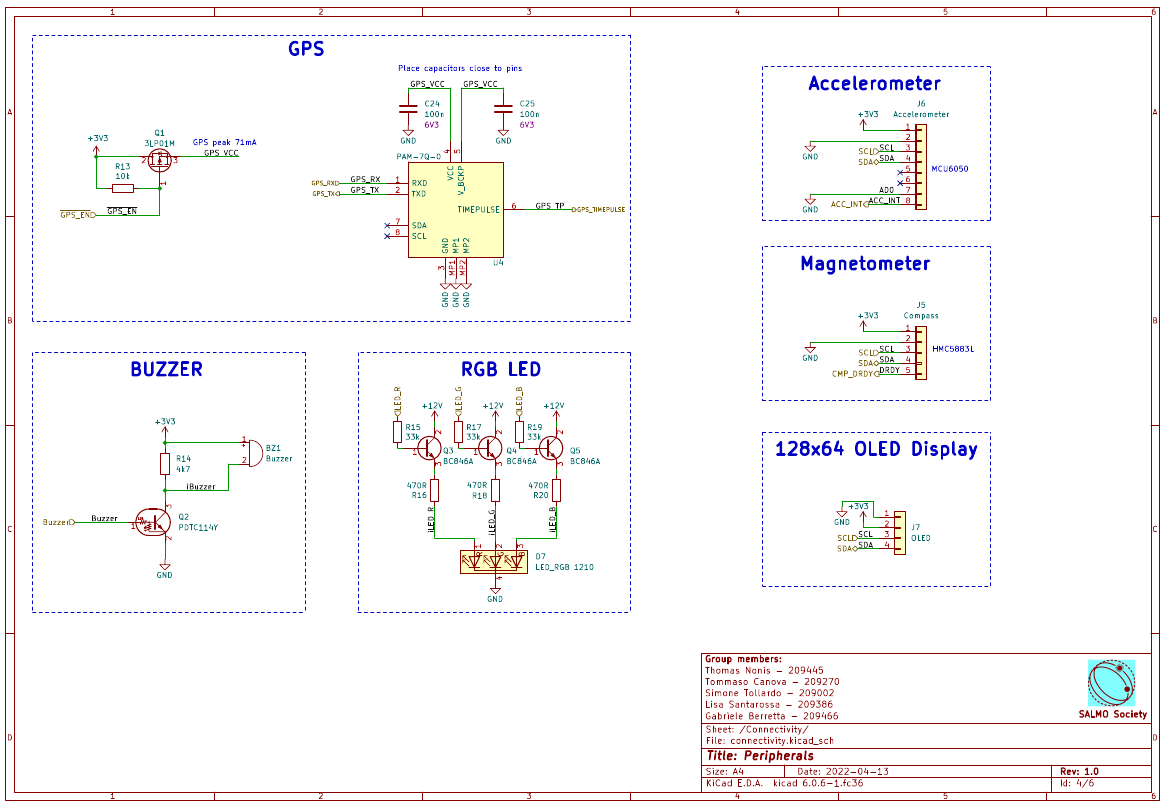
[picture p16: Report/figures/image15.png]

\captionsetup{type=figure}
\captionof{figure}{Foglio "Peripherals" SALMO}
\end{center}

\hypertarget{gps}{%
\subsection{\texorpdfstring{GPS}{GPS}}\label{gps}}

Il dispositivo \emph{GPS} utilizzato è lo \emph{U-BLOX PAM7Q}. Questo
componente permette di interfacciarsi con i satelliti della rete \emph{GPS}
per ottenere le coordinate geografiche del dispositivo, rendendo possibile 
il calcolo della la posizione del sole rispetto al
pannello attraverso l'algoritmo di tracciamento, per poi
stabilire successivamente il movimento dei motori.\\
Il dispositivo utilizza il protocollo standard \emph{NMEA} (ma può
essere configurato anche per utilizzare il protocollo proprietario
\emph{U-BLOX}) per comunicare attraverso la linea seriale.

\begin{center}
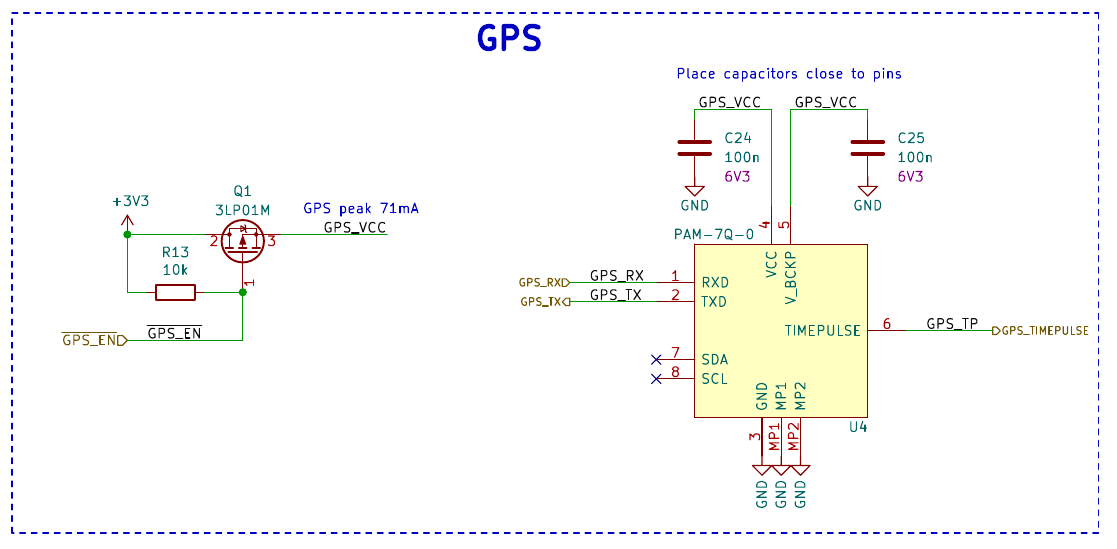
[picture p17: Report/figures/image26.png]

\captionsetup{type=figure}
\captionof{figure}{Circuito del GPS PAM7Q}
\end{center}

\noindent Il dispositivo è alimentato a \emph{3.3V} tramite i pin 4 e 5,
accompagnati dai noti condensatori di decoupling da 100n.
Si noti che $V_{BCKP}$ e $V_{CC}$ sono entrambe connesse alla stessa
alimentazione, in quanto non è stata prevista una batteria tampone. \\
L'alimentazione è interrotta da un transistor \emph{PMOS} (\emph{Q1}) e
viene abilitata solo quando il transistor viene polarizzato
correttamente, ovvero quando $\overline{\rm {GPS\_{EN}}}$ si trova a
livello logico basso. La resistenza da 10kΩ tra gate e source del \textit{PMOS}
serve a mantenere il transistor in cut off quando il pin
$\overline{\rm {GPS\_{EN}}}$ non è pilotato (floating).\\
I pin 1 e 2, cioè \emph{RXD} e \emph{TXD}, sono rispettivamente i pin di
ricezione e trasmissione (dal punto di vista del GPS) per la comunicazione \emph{UART}.\\
Il pin 6 è dedicato al time pulse, ovvero a generare un segnale
periodico programmabile, che di default è impostato ad un \textit{pulse per second} (\textit{PPS}). Il \emph{GPS}
\emph{PAM7Q} presenta anche un interfaccia seriale \emph{I2C} ma, dato
che per il progetto \emph{SALMO} abbiamo scelto un interfacciamento via
\emph{UART,} i pin 7 e 8 (\emph{SDA} e \emph{SCL}) non sono stati connessi.\\
I mounting point \emph{MP1} e \emph{MP2} sono collegati a massa come
indicato da datasheet.

\begin{center}
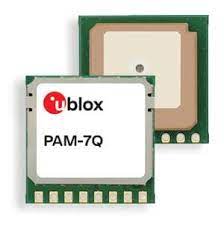
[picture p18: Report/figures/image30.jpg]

\captionsetup{type=figure}
\captionof{figure}{GPS U-Blox PAM7Q}
\end{center}

\hypertarget{magnetometro-ed-accelerometro}{%
\subsection{\texorpdfstring{Magnetometro ed Accelerometro}{Magnetometro ed Accelerometro}}\label{magnetometro-ed-accelerometro}}

Al fine di poter gestire la posizione del pannello mediante controllo ad
anello chiuso abbiamo deciso di sfruttare due sensori: un magnetometro a
3 assi con risoluzione di 12 bit \emph{Honeywell} \emph{HMC5883L} ed un
accelerometro+giroscopio entrambi a 3 assi, a 16 bit \emph{TDK}
\emph{MPU6050}. Entrambi i sensori sfruttano l'interfaccia \emph{I2C} 
ad una velocità massima di 400KHz.\\
Questi, saranno posizionati \textbf{direttamente sul pannello} e
provvederanno a restituire all'algoritmo la sua posizione
rispetto ai due assi di movimento (Azimuth ed Elevazione).\\
Tuttavia, non avendo avuto a disposizione l'accelerometro durante la
fase di assemblaggio, in questa \textit{release} non è fisicamente presente.

\begin{center}
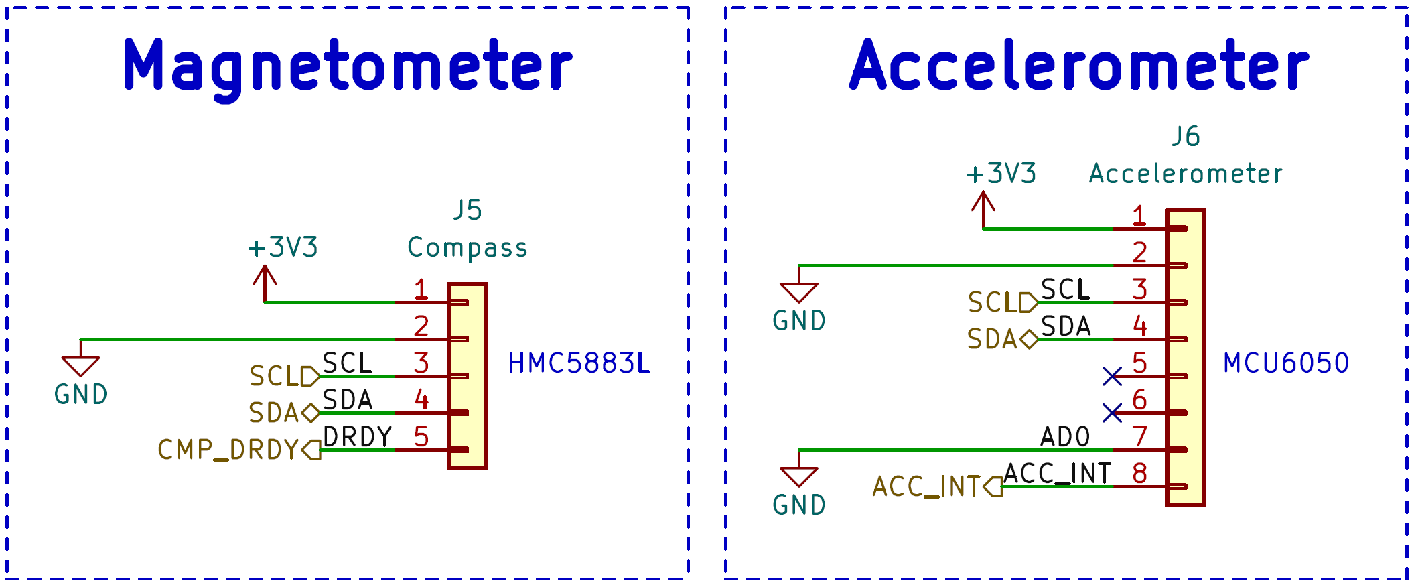
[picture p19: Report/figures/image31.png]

\captionsetup{type=figure}
\captionof{figure}{Connettori Accelerometro e Magnetometro}
\end{center}

\hypertarget{connettore-display-oled}{%
\subsection{\texorpdfstring{Connettore display OLED}{Connettore display OLED }}\label{connettore-display-oled}}

Abbiamo previsto un connettore per un display \emph{OLED 128 x 64} px con
controller integrato \emph{SSD1306}, al fine di presentare all'utente una
immediata visualizzazione dei dati della scheda e del pannello solare. La comunicazione tra il microcontrollore ed il display avviene mediante bus \textit{I2C}. \\
Tuttavia, anche in questo caso, non avendo avuto a disposizione il componente durante la fase
di assemblaggio, in questa \textit{release} non è fisicamente presente.

\begin{center}
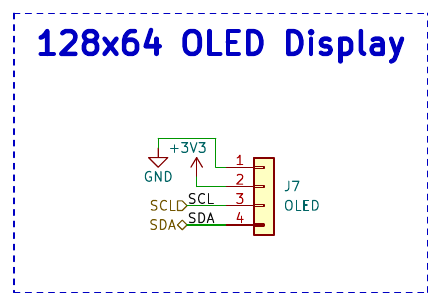
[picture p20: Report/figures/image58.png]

\captionsetup{type=figure}
\captionof{figure}{Connettore display OLED 128x64}
\end{center}

\hypertarget{led-rgb}{%
\subsection{\texorpdfstring{LED RGB}{LED RGB}}\label{led-rgb}}

Per quanto riguarda il circuito del led \emph{RGB 1210} abbiamo commesso
un errore in fase di progettazione: considerandone la configurazione a collettore comune, tra
collettore ed emettitore del transistor cadono circa
$12-(3.3-0.7)=9.4V$!\\
Conseguentemente ai capi dei diodi led cadrà una tensione molto bassa ($12-9.4=2.6V$),
probabilmente nemmeno sufficiente per portarli in conduzione.\\
Purtroppo il problema non è sistemabile, se non modificando il circuito
ed il layout della PCB.\\
Considerando che il componente è del tutto ausiliario abbiamo potuto
testare comunque la scheda senza alcun problema.
Oltre a questo abbiamo commesso un ulteriore errore nell'assegnazione del footprint. 
Abbiamo infatti inserito una sequenza di pin che non è presente in commercio, anche se avessimo progettato il circuito 
correttamente, il montaggio sarebbe comunque risultato impossibile.

\begin{center}
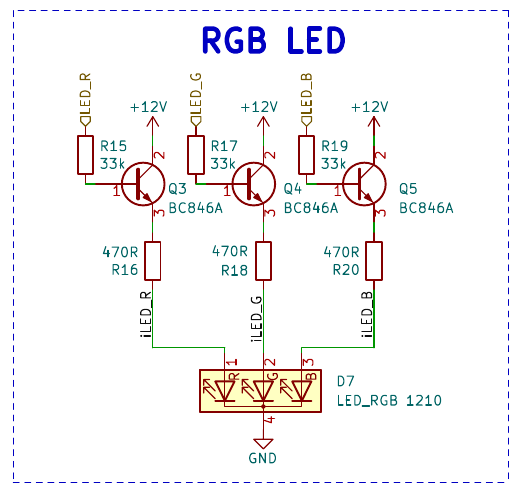
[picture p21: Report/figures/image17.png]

\captionsetup{type=figure}
\captionof{figure}{Circuito led RGB 1210}
\end{center}

\hypertarget{buzzer}{%
\subsection{\texorpdfstring{Buzzer}{Buzzer}}\label{buzzer}}

Abbiamo previsto un buzzer passivo di tipo elettromagnetico per poter
segnalare eventuali stati all'utente e/o errori.\\
Per amplificare il segnale proveniente dall'\textit{RP2040} abbiamo utilizzato un transistor \textit{NPN} con
rete di polarizzazione integrata ed un resistore in parallelo al
cicalino per poter scaricare la tensione imposta dall'induttanza del
buzzer, che altrimenti danneggerebbe il transistor.

\begin{center}
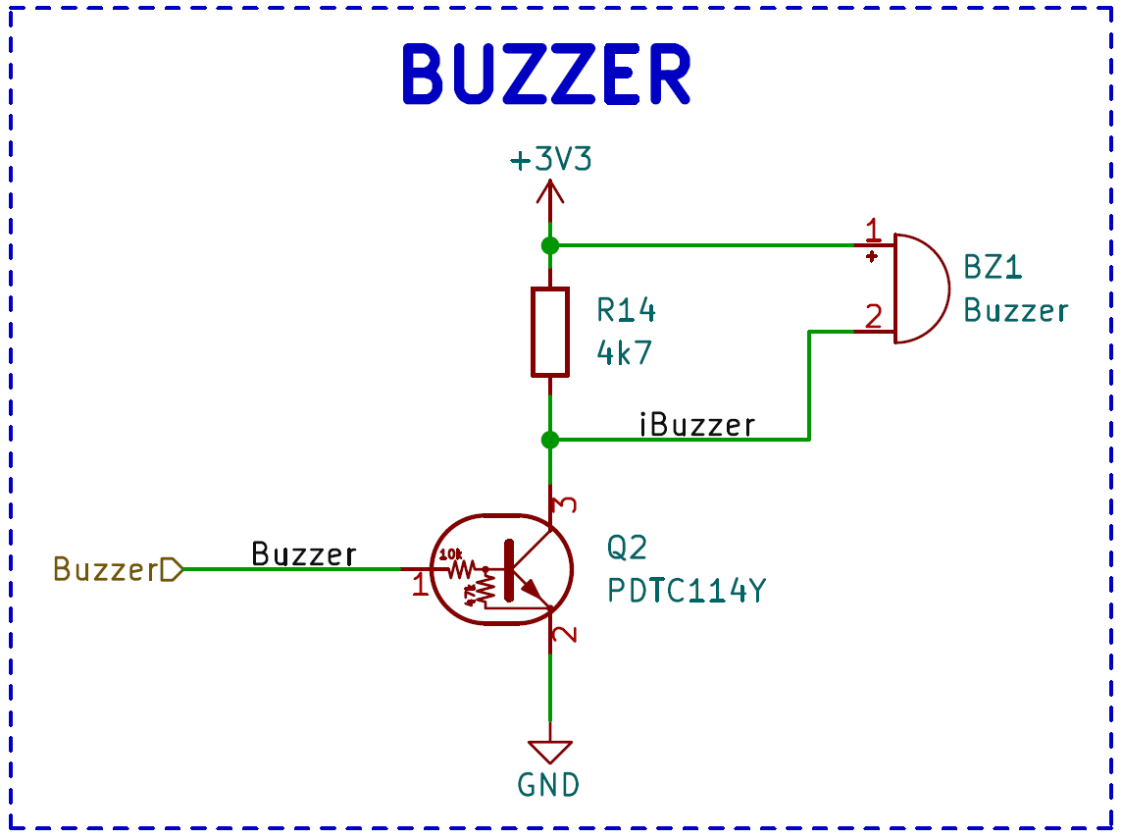
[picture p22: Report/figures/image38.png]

\captionsetup{type=figure}
\captionof{figure}{Circuito buzzer}
\end{center}

\hypertarget{panel-sensing}{%
\section{\texorpdfstring{Panel sensing}{ Panel sensing}}\label{panel-sensing}}

\begin{center}
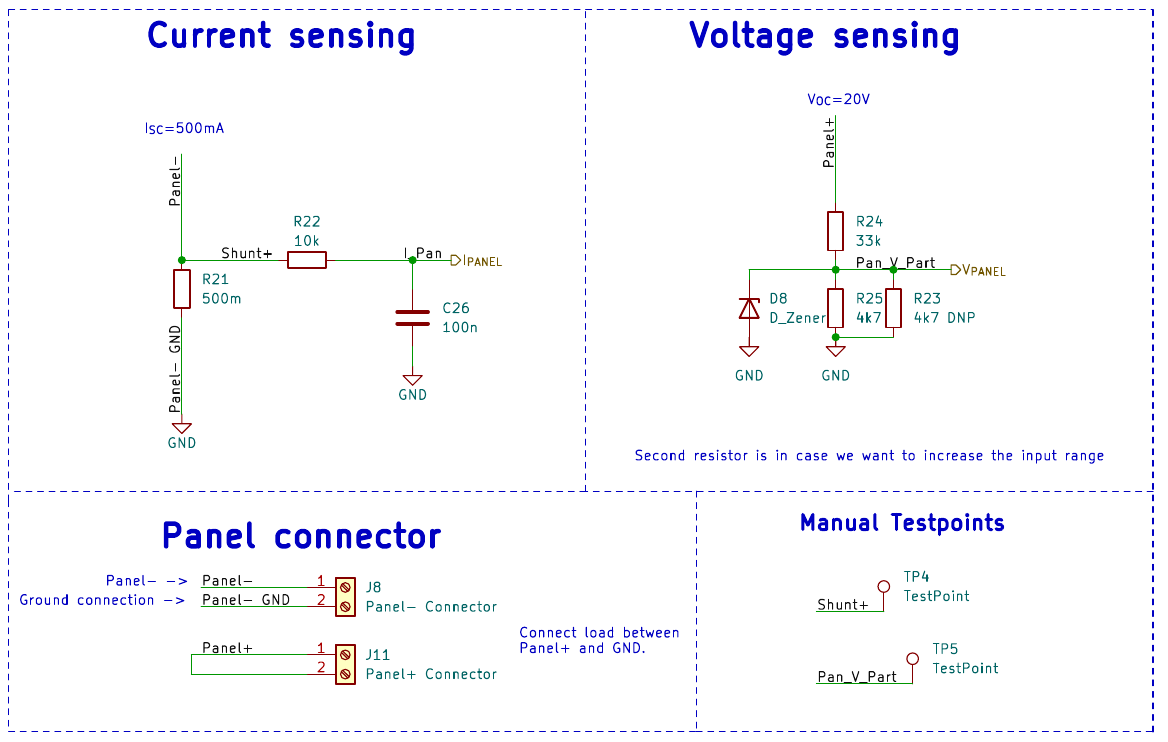
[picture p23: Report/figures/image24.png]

\captionsetup{type=figure}
\captionof{figure}{Foglio "Panel Sensing" SALMO}
\end{center}

\noindent Il panel sensing è stato progettato per la misura dei parametri di
tensione e di corrente del pannello solare. La misura di corrente del
pannello tiene conto di una corrente di cortocircuito (\emph{Isc}) pari
a \emph{500 mA}. Per effettuare la misura è stata posta una resistenza
di \textit{shunt} pari a 500 mΩ per ottenere una misura in configurazione \emph{low-side},
ottenendo così una caduta di tensione ai suoi capi massima di 0.25V che
può essere letta senza problemi dall'ADC dell'\textit{RP2040} (GPIO27, canale 2
dell'ADC).\\
Nella scelta della resistenza di \textit{shunt}, condizionata dal fatto che non
volevamo complicare inutilmente il circuito con degli amplificatori
operazionali, è stato dato maggior peso alla potenza dissipata che allo
sfruttare in maniera ottimale il range dell'ADC.\\
La tensione misurata dall'ADC andrà infatti da 0V (Ipanel=0 A) a 0.25 V
($I_{panel}=I_{sc}=500 mA$) e la potenza dissipata massima sarà quindi
\(R*I^{2}\  = 0.5*0.5^{2} = 0.125\ W\).\\
Avendo un \emph{ADC} a 12 bit, è possibile ottenere una sensibilità di
\(\frac{(Vref - Vss)}{2^{\text{bit}}} = \frac{3.3}{2^{12}} = 805.66\ uV/bit\)
, corrispondente a
\(\frac{(Vref - Vss)}{2^{\text{bit}}*R_{shunt}} = \frac{3.3}{2^{11}*0.5} = 1.6\ mA/bit\).
Data la $V_{max}$ di segnale pari a 0.25 V è possibile sfruttare solamente il
7.6\% dell'intero range disponibile
(\(\frac{V_{ref}}{V_{max}} = \frac{3.3}{0.25} = 7.26\%\))

\begin{center}
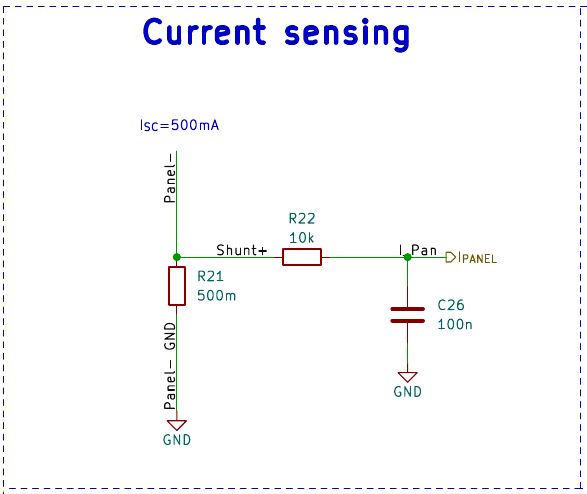
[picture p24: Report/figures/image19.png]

\captionsetup{type=figure}
\captionof{figure}{Circuito Current Sensing SALMO}
\end{center}

\noindent Per la misura di tensione del pannello, non volendo nuovamente
utilizzare amplificatori operazionali o integrati specifici, abbiamo
scelto di utilizzare il metodo del partitore di tensione, posizionando
due resistenze da 33k e 47k per avere un rapporto di partizione di circa
\(\frac{4,7}{4,7 + 33} \simeq \ 0.125\) e quindi un consumo pari a 
\(P=\frac{V^{2}}{R}=\frac{20^{2}}{33k+47k}=5mW\)
se ipotizziamo una tensione di open circuit $V_{oc}$ di 20V.\\
Assumendo le stesse ipotesi, i valori in ingresso al
\textit{GPIO} 26 (canale numero 1 dell'ADC) andranno da 0V a 2.5V (la tensione
massima è comunque fissata dal diodo zener di protezione posto in
parallelo).\\
\[V_{MAXADC}=V_{PANEL}*(\frac{R_{25}}{R_{25}+R_{24}})=20*0.125 =2.5 V\]\\
Nel caso in cui il pannello avesse tensione di open circuit più alta o
volessimo usare più pannelli in serie tra di loro è possibile montare la
resistenza ausiliaria $R_{23}$, che permette di avere un rapporto di
partizione di 0.067.\\
\[V_{MAXADC}=V_{PANEL}*\frac{R_{25}||R_{23}}{(R_{25}||R_{23})+R_{24}}=20*0.067 =1.34 V \]

\begin{center}
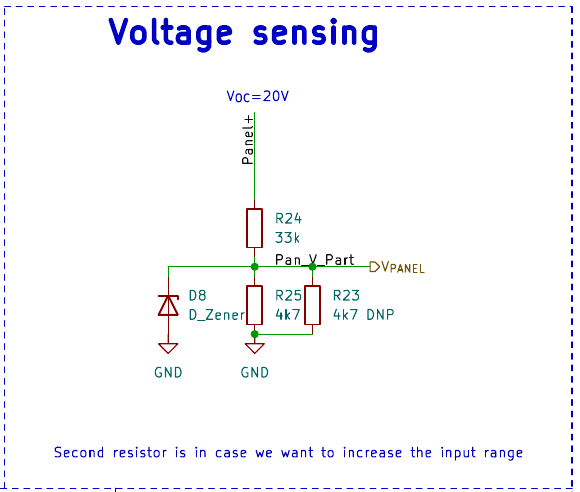
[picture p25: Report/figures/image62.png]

\captionsetup{type=figure}
\captionof{figure}{Circuito Voltage Sensing SALMO}
\end{center}

\noindent In questo foglio abbiamo inoltre deciso di posizionare i connettori per
il collegamento del pannello e del relativo carico/utilizzatore.

\begin{center}

\captionsetup{type=figure}
\captionof{figure}{Connettori per carico e pannello SALMO}
\end{center}

\noindent Abbiamo infine inserito dei \textit{test point} per consentirci di misurare
manualmente la tensione e la corrente del pannello (misurando la caduta
di tensione sulla resistenza di shunt si ottiene
\(i\  = \frac{V_{\text{misurata}}}{R_{21}}\)).

\begin{center}

\captionsetup{type=figure}
\captionof{figure}{Testpoint per la misura manuale di tensione e corrente del pannello}
\end{center}

\hypertarget{actuation}{%
\section{Actuation}\label{actuation}}

\begin{center}

\captionsetup{type=figure}
\captionof{figure}{Foglio "Actuation" SALMO}
\end{center}

\noindent Nella pagina \emph{Actuation} abbiamo inserito i circuiti di controllo per 
i due motori stepper unipolari tramite driver separati a
componentistica discreta e i relativi connettori. I due attuatori hanno
la funzione di orientare il pannello fotovoltaico nella direzione
desiderata, ruotando il pannello attorno agli assi \emph{z} e \emph{y}.\\
Abbiamo scelto i motori passo-passo \emph{Adafruit 918}, con tensione e
corrente nominali rispettivamente di 12V e 500mA, unipolari con
motoriduttore e coppia statica di 250gr/cm.\\
Da evidenziare è la presenza del motoriduttore (\emph{gearbox}) che
permette di ottenere una maggiore risoluzione (da 200 step fino a ben
512) e soprattutto una \emph{maggior coppia statica}; quest'ultima ci
consente di mantenere in posizione il pannello anche quando il motore è
disalimentato così da limitare i consumi totali. Ipotizzando, infatti,
il peso medio di un pannello fotovoltaico da 1W disponibile in commercio
di circa 20gr, una coppia statica di 250gr/cm risulta sufficiente per
consentire di ancorare meccanicamente a dovere il pannello all'asse del
motore.\\
Per giunta, ogni motore essendo di tipo unipolare è dotato di due
avvolgimenti separati con presa intermedia comune, pertanto sono
sufficienti solo quattro transistor per il comando del singolo. Infatti,
a differenza degli stepper bipolari, non è necessario un \emph{h-bridge}
per cambiare il senso di rotazione ma basta invertire l'ordine
sequenziale di attivazione dei transistor. A seguito è illustrato il
circuito base a confronto:

\begin{center}

\captionsetup{type=figure}
\captionof{figure}{Driver per stepper unipolare vs driver per stepper bipolare}
\end{center}

\noindent Il driver è costituito da un \textit{n-mos} pilotato dal \textit{MCU}, con resistenza tra gate e source da 10kΩ 
e resistenza di limitazione tra pin del MCU e gate da 22 Ω. 
La prima funge da \textit{pull-down} nel caso in cui il pin
del MCU sia flottante, al fine di evitare accensioni involontarie del
transistor, pertanto abbiamo scelto il valore di 10kΩ analogamente alle
altre resistenze di \textit{pull-up/down} già presenti nel circuito. La
resistenza da 22Ω invece funge da limitatore di corrente sul ramo che connette il pin \textit{I/O} al
gate del mosfet, introducendo un ritardo nel fenomeno di carica e scarica
della capacità di gate-source del dispositivo, evitando così di bruciare
il pin del \textit{MCU} dato che all'inserzione questa corrente può essere
elevata. Il valore di 22Ω è stato scelto arbitrariamente e fa sì che sul
gate del transistor ci sia una tensione di circa 3.3V (considerando il
partitore tra R26 e R27) quando il pin di output del microcontrollore è
a livello logico alto e, inoltre, determina una costante di
carica/scarica della capacità di ingresso di Q6 di:
%TODO: scarica e carica non hanno la stessa equazione, correggere!
\[\tau = R_{ 26} * C_{gate - source} = 22 \Omega * 7.3nF \approx 160ns\]
Una costante di tempo di tale grandezza è considerata accettabile,
perché ipotizzando una frequenza di lavoro dei \textit{mosfet} di circa 20Hz,
quindi con un periodo di 55ms, permette allo switch di commuttare come
previsto.\\
In parallelo alle sezioni degli avvolgimenti abbiamo inserito un diodo di
\textit{flyback} cosicché all'apertura dello switch non si verifichino \textit{spike} di
tensione critici tra drain e source dello stesso.

\begin{center}

\captionsetup{type=figure}
\captionof{figure}{Circuito driver per un avvolgimento}
\end{center}

\noindent Nel circuito in questione lo switch deve garantire:

\begin{enumerate}
\def\labelenumi{\arabic{enumi}.}
\item
  
  di poter essere pilotato con una tensione di gate di almeno 3.3V
  (livello logico alto dei GPIO del MCU scelto);
  
\item
  
  una corrente di drain di almeno 0.5A (corrente nominale dei motori);
  
\item
  
  una differenza di potenziale tra drain e source di almeno 12V
  (tensione di alimentazione dei motori).
  
\end{enumerate}

\noindent Considerando le specifiche appena elencate abbiamo scelto dei transistor
\textit{Vishay SI2300DS} nel comune package \textit{SOT23}, con tensione di soglia 1.5V e
valori massimi supportati tra drain e source di 30V, tra gate e source
di 12V e una corrente di 3A.

\begin{center}

\captionsetup{type=figure}
\captionof{figure}{Estratto datasheet SI2300DS}
\end{center}

\hypertarget{finalizzazione schematico}{%
\section{Finalizzazione schematico}\label{finalizzazione schematico}}

Una volta terminata la progettazione di tutti i sotto-circuiti della 
nostra scheda abbiamo provveduto a fare un controllo globale. Per questo abbiamo eseguito 
sia un’analisi manuale, valutando tutte le connessioni ed i valori inseriti, sia un’analisi 
automatizzata tramite il \textit{DRC}. Dopo aver riscontrato e risolto qualche inevitabile errore 
abbiamo reputato concluso il processo di progettazione elettrica. A questo punto il \textit{DRC} 
segnala comunque 2 errori ed alcuni warning, che però sono dovuti alle dichiarazioni di alcuni 
pin dei simboli e non influenzano in alcun modo il funzionamento della scheda.

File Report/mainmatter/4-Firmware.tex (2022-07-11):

\chapter{Firmware}

\hypertarget{ambiente-di-sviluppo}{%
\section{Ambiente di sviluppo}\label{ambiente-di-sviluppo}}

Come detto inizialmente, l'intero codice del progetto è \textit{open-source} ed è
visionabile al seguente link:\\
\href{https://github.com/thomasnonis/ppse-2021}{\underline{https://github.com/thomasnonis/ppse-2021}}.\\
Per lo sviluppo del codice abbiamo scelto di lavorare con l'ambiente
\emph{Microsoft Visual Studio Code}, in quanto molto versatile e
continuamente supportato dagli sviluppatori.\\
Per poter utilizzare le librerie del microcontrollore \emph{RP2040} è
stato necessario includere nel progetto il \emph{pico-sdk}, un kit di
sviluppo che permette di implementare le istruzioni \emph{HAL} (Hardware
Abstraction Level) per potersi interfacciare all'hardware del micro ed
alle sue relative periferiche. L'\emph{SDK} non è l'unica libreria a cui abbiamo fatto affidamento, infatti abbiamo aggiunto al progetto
anche \emph{pico-examples} e \emph{picotool}. Con \emph{pico-examples}
siamo riusciti a testare delle funzioni base del microcontrollore ed
allo stesso tempo a capire il processo di compilazione via
\emph{Makefile}, in quanto la libreria era dotata di molteplici esempi
base per ogni periferica offerta dal micro, mentre \emph{picotool} è
stata utilizzata per poter automatizzare il processo di flashing del
codice.\\
Le librerie citate appaiono nel progetto come \emph{submodules}, in
quanto, grazie al software di controllo versione \emph{git} è possibile
tenerle aggiornate senza che siano presenti vincoli legati a delle
specifiche versioni.

\hypertarget{compilazione}{%
\section{Compilazione}\label{compilazione}}

\noindent Durante una fase iniziale di testing abbiamo trovato delle difficoltà
per compilare il codice, in quanto nella documentazione ufficiale non
era ben chiaro come si dovessero scrivere e disporre in modo corretto i
file \textit{CMakeLists}. Con un po' di lavoro abbiamo deciso di strutturare la
compilazione nel seguente modo:

\begin{center}

\captionsetup{type=figure}
\captionof{figure}{Struttura del codice di SALMO}
\end{center}

\noindent Ogni libreria contiene un proprio \textit{CMakeLists} in cui viene specificato il
nome della libreria (linkando i file .c e .h) e vengono \textit{linkate} altre librerie
esterne (come \emph{pico\_stdlib}).

\begin{center}

\captionsetup{type=figure}
\captionof{figure}{CMakeLists della libreria per il calcolo della posizione del sole}
\end{center}

\noindent Dopodichè nel main principale in cui verrà eseguito il codice (presente
in \emph{SALMO.c}), viene definito l'eseguibile (ovvero si linka il file
.c attribuendolo ad un nome), dopodiché si linkano le librerie definite
precedentemente e si includono anche le cartelle in cui queste sono
presenti, per poi opzionalmente decidere se abilitare altri parametri
come \emph{usb output} o \emph{uart output.}

\begin{center}

\captionsetup{type=figure}
\captionof{figure}{CMakeLists di SALMO.c}
\end{center}

\noindent I file \textit{CMakeLists} vengono ``eseguiti'' in ordine gerarchico, per cui è
necessario avere un \textit{CMakeLists} esterno che ha il compito di tenere
traccia di tutti gli altri \emph{CMakeLists} e di definire i parametri
relativi alla versione del \emph{CMAKE} e della versione del compilatore
C e C++. Per compilare il progetto SALMO è sufficiente quindi eseguire
il comando CMake sul file CMakeLists più esterno, producendo così un
Makefile che, una volta eseguito, compilerà autonomamente l'intero
progetto restituendo i file eseguibili necessari per flashare il
microcontrollore.

\begin{center}

\captionsetup{type=figure}
\captionof{figure}{CMakeLists del progetto}
\end{center}

\noindent Per rendere più veloce la fase di compilazione abbiamo deciso di
scrivere tre piccoli script \emph{bash}, situati nella cartella
\emph{src}: \emph{build.sh}, \emph{flash.sh},
\emph{build\_and\_flash.sh}. Lo script di build utilizza \emph{cmake}
per compilare i \emph{Makefile} e salvare i relativi eseguibili dentro
la cartella \emph{build}, mentre quello di flash utilizza
\emph{picotool} per caricare l'eseguibile in formato \emph{.uf2}
direttamente nella \emph{flash} del microcontrollore, anche se il \textit{RP2040}
non si trova in \textit{bootloader mode} (\emph{picotool} riavvia il MCU in
bootloader mode). Infatti se non usassimo \emph{picotool} dovremmo
resettare la scheda tenendo premuto il pulsante di boot per entrare in
bootloader mode, successivamente trascinare il file eseguibile
all'interno della partizione \textit{Mass Storage} del micro, per poi resettarlo
via pulsante. Lo script di \emph{build} è inoltre dotato di un
\emph{flag} opzionale attivabile scrivendo \emph{./build.sh all}, con il
quale viene rimossa l'intera directory di build ed il progetto viene
ricompilato da capo (utile in caso di errori del compilatore non
realmente presenti nel codice). Abbiamo scelto di flashare mediante
l'eseguibile con estensione \emph{.uf2} in quanto, utilizzando questo
tipo di file, è sufficiente copiare l'eseguibile nella partizione di
tipo \textit{Mass Storage} che il \textit{RP2040} offre una volta avviato in bootloader
mode.\\
Come intuibile, il file \emph{build\_and\_flash.sh} esegue sia le
operazioni di compilazione sia l'operazione di flashing.

\hypertarget{algoritmo-per-ottenere-la-posizione-del-sole}{%
\section{Algoritmo per ottenere la posizione del
sole}\label{algoritmo-per-ottenere-la-posizione-del-sole}}

\noindent Al fine di poter pilotare correttamente i motori verso il sole abbiamo
dovuto trovare un modo per convertire i dati ottenuti dal GPS in
elevazione ed azimuth del sole (espressi in gradi). Per approcciare
correttamente il problema abbiamo iniziato a leggere vari \emph{papers}
e relazioni tecniche riguardo ad algoritmi per la rilevazione della
posizione del sole, il primo, forse tra i più datati, è stato \emph{The
astronomical almanac's algorithm for approximate solar position} di
\emph{Joseph J. Michalsky}. Dopo alcune letture abbiamo capito che era
necessario passare tra vari sistemi di riferimento per ottenere le
coordinate del sole, in particolare ci siamo imbattuti nel concetto di
\emph{Julian Date} (giorni passati dalle 12 del 1 Gennaio 4713 B.C.),
coordinate celesti, \emph{GMST} (Greenwich Mean Sidereal Time, un giorno
siderale è 4 minuti più corto di un giorno solare) e \emph{LMST} (Local
Mean Sidereal Time). Nonostante nel paper di \emph{Michalsky} fosse
presente del codice \emph{FORTRAN} per l'implementazione dell'algoritmo,
non lo abbiamo ritenuto abbastanza ``solido'' ed efficiente per il
nostro tipo di applicazione.\\
Per poter verificare la corretta posizione del sole abbiamo utilizzato
questo sito come contro prova dei nostri calcoli:
\href{https://gml.noaa.gov/grad/solcalc/}{\underline{https://gml.noaa.gov/grad/solcalc/}}.

\begin{center}

\captionsetup{type=figure}
\captionof{figure}{Interfaccia web NOAA solcalc}
\end{center}

\noindent Fortunatamente la \emph{NOAA} (National Oceanic and Atmospheric
Administration), oltre a fornire questa interfaccia web, condivide anche
i file \emph{excel} con cui vengono eseguiti i calcoli al fine di
ottenere gli stessi risultati presenti sul loro sito. Di conseguenza,
essendo questo \emph{tool} uno dei pochi affidabili in rete con cui
poter verificare i nostri calcoli, abbiamo deciso di riportare le
formule del file \emph{excel} in codice C per ottenere gli stessi
risultati. I calcoli intermedi non verranno riportati nel dettaglio in
quanto sono computazioni astronomiche che non rientrano nelle tematiche
trattate nel corso.\\
Per la computazione abbiamo fatto riferimento a due strutture dati, una
denominata \emph{Place} in cui viene salvata la data, l'orario e
latitudine e longitudine ``\emph{parsate}'' dal GPS (mediante una
libreria open source), e l'altra, \emph{Position,} in cui vengono
salvati tutti i parametri intermedi ed i risultati finali per il calcolo
della posizione del sole (basato sull'algoritmo della \emph{NOAA}).

\begin{center}

\captionsetup{type=figure}
\captionof{figure}{Struct "Place"}
\end{center}

\begin{center}

\captionsetup{type=figure}
\captionof{figure}{Struct "Position"}
\end{center}

\noindent Per calcolare la posizione esatta del sole infatti i dati contenuti in
\emph{Place} vengono utilizzati per ottenere una \emph{Julian Date},
una \emph{Julian Date} conteggiata a partire dalle 12 del primo Gennaio
2000 e successivamente tutti i parametri intermedi per poi ottenere
elevazione e azimuth del sole. In seguito ad alcuni test abbiamo
riscontrato che siamo in grado di ottenere un'ottima precisione,
addirittura nell'ordine del grado!

\hypertarget{implementazione-software-delle-periferiche}{%
\section{Implementazione software delle
periferiche}\label{implementazione-software-delle-periferiche}}

Tutte le periferiche, a meno di GPS, utilizzano interfaccia di
comunicazione \emph{I2C}.\\
Il protocollo hardware \emph{I2C} prevede due linee seriali di
comunicazione: \emph{SDA} (Serial DAta) per i dati e \emph{SCL} (Serial
CLock) per il clock (la comunicazione I2C è di tipo sincrono).\\
Siccome le linee \emph{SDA} ed \emph{SCL} sono di tipo Open-Drain (o
Open-Collector a seconda della tecnologia utilizzata) sono necessari dei
resistori di pull-up per portare a livello logico alto le linee. Nel
progetto \emph{SALMO}, siccome accelerometro e magnetometro vengono
acquistati sotto forma di moduli commerciali, troviamo già i resistori
di pull-up su di essi, per cui, questi ultimi, verranno dimensionati e
montati direttamente in solo uno dei moduli (verranno quindi rimossi
dagli altri).

\begin{center}

\captionsetup{type=figure}
\captionof{figure}{Esempio di bus I2C}
\end{center}

\noindent La struttura dei driver di HMC5883L e MPU6050 segue una logica ben
precisa, in modo da rendere particolarmente semplice e versatile il
codice:

\begin{itemize}
\item
  
  \textless drivername\textgreater\_defines.h
  
\item
  
  \textless drivername\textgreater\_I2C.h
  
\item
  
  \textless drivername\textgreater\_I2C.c
  
\item
  
  \textless drivername\textgreater.c
  
\item
  
  \textless drivername\textgreater.h
  
\end{itemize}

\noindent Utilizzando questa struttura è possibile innanzitutto separare tutte le
definizioni di registri ed indirizzi in un file header separato
(\textless drivername\textgreater\_defines.h) ed in secondo luogo, forse
vantaggio principale, è possibile dichiarare e definire le funzioni di
lettura e scrittura nel bus I2C in due soli file
(\textless drivername\textgreater\_I2C.h e
\textless drivername\textgreater\_I2C.c) in modo che il vero e proprio
driver (\textless drivername\textgreater.h e
\textless drivername\textgreater.c) rimanga completamente indipendente
dalle funzioni I2C. Questo, è particolarmente vantaggioso perché le
funzioni I2C sono dipendenti dal HAL offerto dall'SDK (e quindi in certo
senso dall'architettura), per cui nel caso in cui volessimo
ri-utilizzare i driver per un'altra architettura (es. STM32) sarebbe
sufficiente modificare solamente le due funzioni di lettura e scrittura
su bus I2C nel file \textless drivername\textgreater\_I2C.c .\\
Il microcontrollore offre due controller I2C: I2C0 ed I2C1. Nel progetto
SALMO viene utilizzato solo uno dei due controller, che viene condiviso
da accelerometro, magnetometro e display.\\
Tutte e 3 le periferiche utilizzano il bus in modalità fast, ovvero a
400KHz.\\
Per effettuare una lettura o la scrittura di un registro di una
periferica nel bus è necessario che il master invii un messaggio
specifico determinato dal protocollo I2C: bit di start, 7, 8 oppure 10
bit di indirizzo (HMC5883L utilizza 8 bit, mentre MPU6050 e SSD1306
utilizzano 7 bit di indirizzo), un bit che indica lettura o scrittura,
un bit di acknowledge da parte dello slave, e successivamente 8 bit di
dato (ad esempio il registro da leggere o il registro in cui si vuole
scrivere, seguito di nuovo da un bit di acknowledge. È possibile inviare
N blocchi da 8 bit seguiti dal bit di acknowledge dopo il bit di
read/write (anch'esso seguito da un bit di acknowledge).

\begin{center}

\captionsetup{type=figure}
\captionof{figure}{Data frame protocollo I2C}
\end{center}

\noindent Nel caso, ad esempio, in cui si voglia scrivere il contenuto di un
registro del MPU6050 è sufficiente inviare: bit di start, 7 bit di
indirizzo (LSB configurabile), bit di read (es. 0 1101000 1) che saranno
seguiti da un bit di acknowledge ed infine invieremo gli 8 bit
dell'indirizzo su cui vogliamo scrivere (es. 00111011). Successivamente
invieremo, dopo aver ricevuto l'acknowledge, i dati che vogliamo
scrivere.\\
Nel caso della lettura invece, è necessario ripetere la procedura
illustrata precedentemente fino all'invio dell'indirizzo del registro
(in questo caso da leggere) ed inviare un bit di start seguito
dall'indirizzo dello slave ed infine un bit di read. La periferica slave
invierà finalmente, sempre dopo il bit di acknowledge, il contenuto del
registro richiesto.

\begin{center}

\captionsetup{type=figure}
\captionof{figure}{Data frame esempio lettura I2C}
\end{center}

\begin{center}

\captionsetup{type=figure}
\captionof{figure}{Funzioni di write e read I2C (driver MPU6050)}
\end{center}

\noindent Per quanto concerne l'implementazione software del display OLED, abbiamo
deciso di utilizzare la libreria già presente negli SDK di Raspberry
Pico (seppur per nulla completa). Sottolineiamo che attualmente il
driver di questa periferica non è stato completato poiché, non avendola
sotto mano, abbiamo deciso di prioritizzare il resto del lavoro.\\
Un altro protocollo di comunicazione utilizzato nel progetto è
\emph{UART} (\emph{Universal Asynchronous Receiver-Transmitter})che, come
visto nel primo modulo del corso, permette il trasferimento e ricezione
di dati in seriale ad un tasso di velocità [bit/s] fissato, detto baud
rate. Abbiamo inserito la configurazione \emph{UART} nel modulo
\emph{PAM7Q.c}, file in cui vengono inizializzati i pin RX e TX, e
vengono settati tutti i parametri necessari a comporre il data frame,
assumendo la seguente configurazione:

\begin{itemize}
\item
  
  Hardware flow: no
  
\item
  
  Baud rate: 9600 bit/s
  
\item
  
  Bit di dato: 8
  
\item
  
  Bit di stop: 1
  
\item
  
  Bit di parità: no
  
\end{itemize}

\begin{center}

\captionsetup{type=figure}
\captionof{figure}{Pacchetto gestito con comunicazione UART}
\end{center}

\noindent Il modulo GPS comunica in \emph{UART}, codificando i messaggi con standard NMEA 1803
(National Marine Electronics Association). Per la lettura dei dati viene
popolato un buffer, di lunghezza 100 bytes, con ogni carattere ricevuto.
All'occorrenza del carattere \emph{``\textbackslash n''} la stringa
ricevuta viene salvata in un array di supporto, il buffer viene
successivamente svuotato e ricomincia la lettura per un numero di volte pari a
GPS\_MAX\_SENTENCES. Abbiamo inoltre deciso di comunicare con il
GPS in \textit{polling}, anzichè utilizzare un interrupt, poiché interagendo con
il modulo ad intervalli ben definiti la seconda opzione avrebbe portato
ad un inutile \textit{overhead} a causa della continua interruzione del
microcontrollore rispetto alle sue principali task.\\
Per tradurre le stringhe NMEA in informazioni utili alla struttura
\emph{Place}, definita nel modulo dell'algoritmo, è stata utilizzata una
libreria open source in grado di analizzare questi messaggi (vedasi
bibliografia). Tipicamente una stringa NMEA è composta nel seguente
modo:\\
\[\$ PREFISSO,dato1,dato2\ ...\ datoN - 1,datoN*CHECKSUM\]\\
In base al tipo di prefisso vengono trasferiti diversi tipi di dati, per
la nostra applicazione abbiamo fatto principale affidamento ai due
messaggi:

\begin{itemize}
\item
  
  \$\emph{GPRMC}: fornisce la data (Anno, Mese, Giorno)
  
\item
  
  \$\emph{GPGGA}: fornisce tempo (Ore, Minuti, Secondi), Latitudine,
  Longitudine.
  
\end{itemize}

\noindent Abbiamo valutato la correttezza del parsing utilizzando un tool online
(vedasi bibliografia)

\hypertarget{implementazione-driver-motori}{%
\section{Implementazione driver
motori}\label{implementazione-driver-motori}}

\noindent Il firmware di controllo dei motori è stato sviluppato partendo da una
libreria già esistente e open source disponibile su github, composta
da due file: \emph{pico\_stepper.h} e \emph{pico\_stepper.c}.\\
Nel primo è definita la \emph{struct} necessaria per inizializzare ogni
motore, mentre nel secondo gli \emph{header} delle funzioni implementate.\\
Per interfacciarsi ai motori è stato necessario inizializzare la
\emph{struct} e i pin fisici delle 4 fasi e definire la velocità di
rotazione del motore. Successivamente i motori vengono comandati
mediante la funzione \emph{step()}, che implementa il metodo ``wave
drive'', nel quale le fasi vengono pilotate in modo sequenziale da
un'onda quadra con un duty cycle del 25\%. La forma d'onda non è
generata tramite la periferica \emph{pwm} bensì in \emph{bit banging}
per semplicità di scrittura firmware dato che non erano necessarie
velocità elevate di commutazione.

\begin{center}

\captionsetup{type=figure}
\captionof{figure}{Fasi per pilotaggio stepper unipolare}
\end{center}

\begin{center}

\captionsetup{type=figure}
\captionof{figure}{Output SALMO su oscilloscopio}
\end{center}

\hypertarget{funzionamento-generale-del-codice}{%
\section{Funzionamento generale del
codice}\label{funzionamento-generale-del-codice}}

\begin{center}

\captionsetup{type=figure}
\captionof{figure}{Flowchart del funzionamento del codice}
\end{center}

\noindent Come prima cosa vengono inizializzate le varie periferiche e moduli
ovvero:

\begin{itemize}
\item
  
  UART
  
\item
  
  USB CDC
  
\item
  
  I2C
  
\item
  
  Accelerometro
  
\item
  
  Magnetometro
  
\item
  
  Motore stepper
  
\end{itemize}

\noindent Dopodiché il microcontrollore entra in loop infinito in cui vengono
controllati degli input e delle variabili interne impostate dai timer.
Sono presenti tre timer che scandiscono:

\begin{itemize}
\item
  
  Lettura input gps (ogni 4 secondi)
  
\item
  
  Aggiornamento della posizione del motore (ogni 10 secondi)
  
\item
  
  Aggiornamento posizione del sole mediante algoritmo (ogni 4 secondi)
  
\end{itemize}

\noindent Entrati nel loop infinito viene controllato, tramite interrupt, se il
pulsante di \emph{``Go home''} (\emph{SW3}) viene premuto; qualora
succeda, i motori vengono azionati per dirigere il pannello verso il
\emph{Nord} ottenuto dalla bussola ed a 45° di elevazione (tilt).
Successivamente viene verificato, sempre tramite interrupt, se il
pulsante di ``Tracking enable/disable'' (\emph{SW4}) viene premuto. In
questo caso il flag di tracking viene abilitato o disabilitato in base
al numero di iterazioni col pulsante, infatti ad ogni pressione il flag
viene negato, pertanto dopo averlo premuto una volta il motore rimarrà
in tracking mode e se il pulsante verrà azionato di nuovo il flag di
tracking verrà disabilitato. Alla scadenza del timer relativo al
tracking, se il flag dovuto al pulsante è abilitato, viene aggiornata la
posizione del motore. Dopodichè viene controllato se il timer relativo
alla lettura del gps è terminato, in caso affermativo viene eseguita la
lettura via \textit{UART} ed il relativo parsing. Infine viene controllato se il
timer relativo alla posizione del sole è scaduto, e di conseguenza viene
o meno eseguito il calcolo della posizione del sole basandosi sui dati
ottenuti dal GPS. Il programma poi ritorna nel loop principale e
continua il controllo delle variabili.\\
A causa della mancanza di accelerometro, pannello e struttura di
supporto per i motori, ulteriori \emph{feature} verranno implementate in
futuro.

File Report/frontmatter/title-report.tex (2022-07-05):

\begin{titlepage}

\begin{center}

%% Print the title
{\makeatletter
\largetitlestyle\fontsize{35}{35}\selectfont\@title
\makeatother}

%% Print the subtitle
{\makeatletter
\ifdefvoid{\@subtitle}{}{\bigskip\bigskip\qquad \; \titlestyle\fontsize{15}{15}\selectfont\@subtitle}
\makeatother}

\bigskip
\bigskip

by
 
\bigskip
\bigskip

%% Print table with names and student numbers
\setlength\extrarowheight{2pt}
\begin{tabular}{lc}
    Student Name & Student Number \\\midrule
    Lisa Santarossa & 209386\\
    Thomas Nonis & 209445\\
    Tommaso Canova & 209270\\
    Simone Tollardo & 209002\\
    Gabriele Berretta & 209466 \\
\end{tabular}

\vfill

%% Print some more information at the bottom
\begin{tabular}{ll}
    Docente: & Michele Corrà \\
    Dipartimento: & Dipartimento di Ingegneria e Scienza dell'Informazione
\end{tabular}

\bigskip
\bigskip

\end{center}

\end{titlepage}

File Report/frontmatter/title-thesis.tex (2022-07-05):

\begin{titlepage}

\begin{center}

%% Print the title
{\makeatletter
\largetitlestyle\fontsize{45}{45}\selectfont\@title
\makeatother}

%% Print the subtitle
{\makeatletter
\ifdefvoid{\@subtitle}{}{\bigskip\titlestyle\fontsize{30}{30}\selectfont\@subtitle}
\makeatother}

\bigskip
\bigskip

by

\bigskip
\bigskip

%% Print the name of the author
{\makeatletter
\largetitlestyle\fontsize{25}{25}\selectfont\@author
\makeatother}

\bigskip
\bigskip

\vfill

\bigskip
\bigskip

\end{center}

\end{titlepage}

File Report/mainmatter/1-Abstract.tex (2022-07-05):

\chapter{Abstract}

La seconda parte del corso di Progettazione e Prototipazione di Sistemi
Elettronici prevede la completa progettazione di una scheda elettronica
che, nel nostro caso, ha come scopo quello di orientare in maniera
ottimale un pannello fotovoltaico verso la posizione del sole nel
cielo.\\
Per rendere più funzionale possibile la scheda \textit{Solar Azimuth and eLevation Motorized lOcator} (``\emph{SALMO}'') si è deciso di
rendere il tutto indipendente dalla posizione geografica, dall'orientamento del pannello fotovoltaico ed ovviamente
% //TODO : rivedere
dall'orario e dal giorno dell'anno. Il movimento del pannello è stato
progettato in modo che la sua posizione sia sempre il più possibile
perpendicolare ai raggi solari affinché la potenza generata dal pannello
possa essere sempre massima.\\
Per raggiungere l'obiettivo sono state stilate le seguenti specifiche:
due motori passo-passo unipolari per il movimento sui due assi (Azimuth
e Elevation), \emph{GPS} per rilevare la posizione geografica,
magnetometro ed accelerometro per il feedback della posizione del
pannello, circuiti di misura per tensione e corrente del pannello,
display \textit{OLED} per la visualizzazione dei dati mediante interfaccia utente
ed ovviamente un pannello fotovoltaico.
La progettazione della scheda è stata svolta in maniera precisa,
rigorosa ed organizzata, seguendo quindi dei passi ben definiti in modo
che ogni membro del team potesse lavorare parallelamente agli altri ed
allo stesso tempo contribuire al lavoro di tutti senza perdere step
fondamentali.\\
Inizialmente, facendo uso dei datasheet, abbiamo studiato
approfonditamente le caratteristiche del microcontrollore \emph{RP2040}
e dei componenti principali della scheda, al fine di poter progettare la
\emph{PCB} in maniera più consapevole. Ogni studente del corso ha poi
esposto alcune caratteristiche del microcontrollore, a partire dalla
memoria fino alla struttura fisica passando per le varie interfacce di
comunicazione, \emph{l'ADC}, i \emph{GPIO} e l'alimentazione.\\
Ogni gruppo ha poi concordato con il professore il progetto da
realizzare, fissando delle scadenze per la consegna dei vari schematici
ed infine per la \emph{BOM}.\\
Sono state decise inoltre delle specifiche di progetto uguali per ogni
gruppo, come ad esempio le dimensioni della scheda (10x6 cm) ed il
regolatore di tensione, in modo da avere delle BOM più uniformi
possibili, senza decine di componenti alternativi non necessari. Dopo
l'avvio vero e proprio del progetto in autonomia, le lezioni svolte in
classe o in laboratorio erano principalmente volte alla correzione, alla
revisione ed al debugging, facendo sì che ogni dubbio potesse essere
chiarito immediatamente.\\
Finito lo sbroglio circuitale siamo passati alla generazione e all'invio
dei file gerber al Professore, che ha successivamente provveduto a
spedire questi ultimi al produttore. Analogamente, dopo aver completato
la \emph{BOM}, questa è stata inviata al Professore per il conseguente
acquisto del materiale necessario. In seguito all'arrivo delle
\emph{PCB} e dei componenti essenziali, abbiamo iniziato l'assemblaggio
sfruttando la strumentazione offerta dal laboratorio di elettronica
presente all'interno del FabLab. Dopo aver completato l'assemblaggio,
realizzato gran parte del firmware, e svolto test a freddo prima (senza
alimentazione) ed a caldo successivamente (con +5V USB e +12V), possiamo
affermare che, benché ci siano ancora dei componenti mancanti, il
prototipo è completamente funzionante (a meno di un piccolo errore, vedasi
cap. \protect\hyperlink{led-rgb}{\underline{LED RGB}} ).
Tutto il progetto della \emph{PCB} è stato svolto utilizzando il
software open-source \emph{KiCad 6.0}, mentre per la progettazione del firmware
abbiamo utilizzato l'\emph{IDE VS Code} e la compilazione manuale via
\emph{CMake}.\\
Per la gestione dell'intero progetto abbiamo deciso di avvalerci di un
\emph{VCS (Version Control System)}: git.\\
La repository è hostata su GitHub e può essere visionata cliccando sul
seguente link:\\
\href{https://github.com/thomasnonis/ppse-2021}{\underline{https://github.com/thomasnonis/ppse-2021}}.

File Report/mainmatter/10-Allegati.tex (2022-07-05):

\chapter{Allegati}

\hypertarget{gerbers}{%
\section{Gerbers}\label{gerbers}}
Si allegano i seguenti documenti, in scala 1:1, nell'ordine specificato:

\begin{enumerate}
    \item B\_Cu
    \item B\_Mask
    \item B\_Silkscren
    \item Edge\_Cuts
    \item F\_Cu
    \item F\_Mask
    \item F\_Paste 
    \item F\_Silkscreen
    \item Drill map (non in scala)
\end{enumerate}

\includepdf[pages={1}]{figures/gerbers/PPSE_2021-B_Cu.pdf}
\includepdf[pages={1}]{figures/gerbers/PPSE_2021-B_Mask.pdf}
\includepdf[pages={1}]{figures/gerbers/PPSE_2021-B_Silkscreen.pdf}
\includepdf[pages={1}]{figures/gerbers/PPSE_2021-Edge_Cuts.pdf}
\includepdf[pages={1}]{figures/gerbers/PPSE_2021-F_Cu.pdf}
\includepdf[pages={1}]{figures/gerbers/PPSE_2021-F_Mask.pdf}
\includepdf[pages={1}]{figures/gerbers/PPSE_2021-F_Paste.pdf}
\includepdf[pages={1}]{figures/gerbers/PPSE_2021-F_Silkscreen.pdf}
\includepdf[pages={1}]{figures/gerbers/PPSE_2021-drl_map.pdf}

\section{BOM}\label{gerber}
Si allega di seguito la distinta base con tutti i componenti presenti sulla scheda
\includepdf[pages={1-}]{figures/BOM_PPSE.pdf}

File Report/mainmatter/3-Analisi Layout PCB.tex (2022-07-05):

\chapter{Analisi del Layout PCB}

Una volta terminato il progetto dello schematico e verificata la sua
correttezza, siamo passati allo sbroglio circuitale. Abbiamo quindi
esportato la netlist da \emph{eeschema} per poi importarla in
\emph{pcbnew}, popolando il progetto con i footprint di tutti i
componenti.

\hypertarget{layout}{%
\section{Layout}\label{layout}}

Come primo passo abbiamo raggruppato i vari componenti per sezione
circuitale (alimentazione, microcontrollore, controllo motori,
ecc\ldots) in modo da avere un primo ordine.\\
Fino a questo punto non abbiamo posto alcun riguardo verso la posizione
dei componenti, ma abbiamo semplicemente effettuato una suddivisione
funzionale. Con il passo successivo abbiamo invece collocato, per
ciascun blocco circuitale, ogni componente nel modo che più ci è
sembrato adeguato, tenendo in mente gli aspetti elettrici (per esempio
il posizionamento del GPS lontano dalla sezione di potenza e dal
microcontrollore), di distanziamento, di funzionalità (per esempio
posizionamento di connettori e pulsanti), di comodità per l'utente
finale ed infine di estetica.\\
Per quanto riguarda la sezione legata al microcontrollore abbiamo
posizionato, in ordine di priorità:

\begin{enumerate}
\def\labelenumi{\arabic{enumi}.}
\item
  
  il quarzo con i suoi condensatori ed il suo resistore il più vicino
  possibile ai pin \textit{XIN} e \textit{XOUT};
  
\item
  
  i condensatori di decoupling più vicini possibile ai pin di
  alimentazione;
  
\item
  
  la memoria flash;
  
\item
  
  i resistori di terminazione della linea USB.
  
\end{enumerate}

\begin{center}

\captionsetup{type=figure}
\captionof{figure}{Primo posizionamento componenti principali foglio Control}
\end{center}

\noindent Il fatto di posizionare i componenti il più vicino possibile ai relativi
pin è necessario per ridurre di quanto possibile l'impedenza della linea
di alimentazione, e quindi la lunghezza del percorso del segnale.
Maggiore è la lunghezza del percorso tra condensatore e pin e maggiore
sarà l'induttanza parassita della traccia, che porta a problemi di
integrità di segnale quando si ha a che fare con segnali ad alta velocità.
Considerando a titolo di esempio una linea di alimentazione,
l'induttanza parassita è contrastata dalla presenza dei condensatori di
decoupling. In questo modo siamo in grado fornire un percorso a bassa
impedenza tra condensatore e pin del MCU, perciò la restante lunghezza
che va dal condensatore al pin di alimentazione deve rimanere il più
breve possibile. Si noti che ai fini del calcolo si deve considerare sia
la linea di andata (es: alimentazione) che quella di ritorno (GND).\\
Per quanto riguarda la sezione di controllo dei motori abbiamo
posizionato i connettori, i transistor, i diodi ed i resistori di
polarizzazione in modo da ridurre al minimo le tracce necessarie e da
allineare il tutto per renderlo il più esteticamente bello possibile.

\begin{center}

\captionsetup{type=figure}
\captionof{figure}{Primo posizionamento componenti driver motori stepper}
\end{center}

\noindent Parlando dello stadio di alimentazione, abbiamo posizionato tutti i
componenti in modo da minimizzare il numero di tracce necessarie e da
facilitare il routing di tracce di grande spessore. Abbiamo rivolto
particolare attenzione al regolatore a commutazione, cercando di rendere
il nodo di switching più piccolo possibile per ridurre al minimo il
\textit{ripple}.

\begin{center}

\captionsetup{type=figure}
\captionof{figure}{Primo posizionamento componenti foglio Power}
\end{center}

\noindent Le restanti sezioni non includono componenti particolarmente critici,
quindi il posizionamento è stato fatto seguendo il principio di
semplicità di routing delle tracce e di bellezza estetica.\\
A questo punto, dopo aver ottenuto un insieme di diversi blocchi
circuitali, abbiamo provato a posizionarli in modo da capire che
dimensioni imporci come limite per la scheda ed abbiamo appurato che
100x60mm fosse una misura adeguata per contenere il tutto.\\
Avendo definito le dimensioni siamo passati alla creazione del disegno
del contorno della scheda sul layer \textit{Edge.Cuts}, introducendo un
arrotondamento degli angoli per fini puramente estetici. Successivamente
abbiamo disegnato i rettangoli di riempimento, assegnandoli alla net di
GND e con priorità minima per entrambi i layer, in modo che coprissero
la scheda intera.\\
Abbiamo quindi posizionato i blocchi circuitali discussi in precedenza,
non prima di aver posizionato i fori di montaggio ed i \textit{fiducials},
facendo in modo di avere i connettori lungo il bordo. Anche il \textit{GPS} è
stato posizionato in un angolo in modo da tenerlo il più lontano
possibile da ogni altro componente; sotto il suo ingombro abbiamo
inserito anche una \emph{keepout zone}, come richiesto da datasheet.

\begin{center}

\captionsetup{type=figure}
\captionof{figure}{Prima bozza piazzamento componenti}
\end{center}

\hypertarget{routing}{%
\section{Routing}\label{routing}}

\noindent Una volta definite le posizioni dei vari componenti siamo passati alla
fase di routing, cominciando dalle linee particolarmente sensibili e poi
quelle di alimentazione. Prima di iniziare abbiamo creato una serie di
dimensioni predefinite per le tracce:

\begin{itemize}
\item
  
  0.2mm per il \textit{fanout} del microcontrollore
  
\item
  
  0.3mm per le linee di segnale in generale
  
\item
  
  0.5mm per le linee di alimentazione
  
\item
  
  0.8mm per le linee di alimentazione dei motori
  
\end{itemize}

\noindent Abbiamo inoltre creato due dimensioni predefinite per le \textit{vias} (diametro
pad/diametro foro):

\begin{itemize}
\item
  
  0.55mm/0.25mm per le linee di segnale
  
\item
  
  0.8mm/0.4mm per le linee di alimentazione
  
\end{itemize}

\noindent Una volta preparato l'ambiente di lavoro abbiamo cominciato a collegare
tutte le linee di alimentazione, partendo prima da quelle più corte che,
per esempio, collegano un pin di un dispositivo al relativo condensatore
di decoupling, per effettuare solo alla fine i collegamenti più lunghi
facendo in modo di lasciare sufficiente spazio per le linee di segnale.\\
Per quanto riguarda il routing dell'alimentazione vogliamo sottolineare
3 accorgimenti che abbiamo preso:

\begin{itemize}
\item
  
  per le tracce che vanno dal connettore del pannello solare allo shunt
  per misurare la corrente, abbiamo deciso di utilizzare uno spessore di
  1mm, in modo da ridurne al minimo la resistenza;
  
\item
  
  per effettuare il fanout del microcontrollore abbiamo utilizzato
  tracce da 0.2mm per allontanarsi dai pin, per poi allargarle il prima
  possibile a 0.3mm;
  
\item
  
  per il routing della linea di alimentazione a 12V per il controllo dei
  motori abbiamo utilizzato per quanto possibile i poligoni di
  riempimento, assegnando la net 12V ed impostando la priorità ad 1.
  
\end{itemize}

\begin{center}

\captionsetup{type=figure}
\captionof{figure}{Prima bozza routing tracce}
\end{center}

\noindent Una volta concluso il routing delle linee di alimentazione siamo passati
alle restanti linee di segnale iniziando dal fanout del
microcontrollore, anche in questo caso partendo con tracce da 0.2mm per
poi allargarle a 0.3mm.\\
Abbiamo considerato per primi i segnali critici, ovvero le linee del
quarzo, quelle per la trasmissione \textit{QSPI} della flash e quelle
differenziali per l'USB. Sebbene non sia di apprezzabile effetto dal
punto di vista funzionale, abbiamo voluto provare, a titolo di esercizio
personale, il tool di \emph{length matching} per rendere le linee
differenziali D+ e D- dell'USB più simili possibile in termini di
lunghezza. Questo è stato fatto, perché abbiamo riscontrato alcune
difficoltà nell'utilizzo del router differenziale, che avrebbe gestito
il \emph{length matching} in autonomia.\\
Avendo definito le tracce critiche siamo poi passati al fanout e al
routing dei restanti segnali. Durante questo processo abbiamo iterato
più volte spostando le assegnazioni di alcuni pin del microcontrollore,
grazie alle matrici di assegnazione dei GPIO, in modo da trovare le
posizioni ottimali.\\
Questa parte dello sbroglio è stata la più complessa a causa della
necessità di avere molti dispositivi vicini al microcontrollore e alla
ridotta \emph{clearance} tra i pin.



\begin{center}
\captionsetup{type=figure}
\captionof{figure}{Primo risultato routing PCB}
\end{center}

\noindent Terminato il routing di tutte le tracce abbiamo fatto un'analisi per
cercare eventuali sviste o errori commessi, sia facendo un'ispezione
visiva, sia utilizzando il \textit{DRC}. Prevedibilmente abbiamo riscontrato
qualche errore che abbiamo prontamente corretto senza troppe difficoltà.\\
Anche dopo queste correzioni il \textit{DRC} restituisce alcuni errori, che però
sono previsti e non causano problemi nella realizzazione. Questi sono di
due tipi, il primo è il \emph{Courtyards overlap} per i componenti che
stanno vicino al \textit{GPS}, mentre il secondo è l' \emph{Items not allowed} ed
è dovuto a come sono stati realizzati i footprint dei fiducials.\\
Il primo lo si può ignorare, perché in realtà il \textit{GPS} sarà montato su un
header rialzato e quindi la superficie del PCB sarà libera da
occlusioni. Il secondo errore invece è dovuto al fatto che il footprint
dei \textit{fiducials} è stato realizzato con due pad che sovrappongono una
\emph{keepout zone}, questo però è comunque un effetto desiderato,
quindi possiamo ignorarlo.

\hypertarget{finitura}{%
\section{Finitura}\label{finitura}}

\noindent Arrivati a questo punto abbiamo appurato che l'aspetto elettrico della
scheda era corretto, quindi ci siamo concentrati sugli aspetti estetico
e utilitario.\\
Prima di tutto abbiamo aggiunto un pad di GND a lato scheda per poter
collegare una pinza a coccodrillo in modo da semplificare le misurazioni
per il debug hardware. Poi abbiamo fatto in modo di posizionare, sul
layer \textit{silkscreen} tutti i \textit{refdes} dei componenti, in modo tale che fossero
ordinati e ben visibili, facendo particolare attenzione, per quanto
possibile, a non posizionarli sopra vias che avrebbero causato
potenziali problemi di lettura.

\begin{center}

\captionsetup{type=figure}
\captionof{figure}{Esempio Silkscreen SALMO}
\end{center}

\noindent Sistemati tutti i \textit{refdes} abbiamo aggiunto sui layer di \textit{silkscreen}
ulteriori descrizioni per chiarire le funzioni dei connettori e per
aggiungere informazioni utili. In particolare abbiamo aggiunto 
l’indicazione di polarità sul connettore di alimentazione e, ad ogni
connettore il suo nome e, sul retro, la descrizione di ogni pin. Per i
connettori di espansione e debug non c'era spazio a sufficienza, quindi
abbiamo creato sul retro una grafica apposita composta da una tabella,
che rappresenta la funzione di ogni pin, e da un segmento di retta che
riconduce la tabella al connettore a cui fa riferimento.\\
Abbiamo successivamente aggiunto, sempre sul retro, il titolo del
progetto con il nome del corso, nomi, cognomi e matricole dei membri del
gruppo e data e numero di revisione.

\begin{center}

\captionsetup{type=figure}
\captionof{figure}{Vista del retro della PCB SALMO}
\end{center}

\noindent Per poter facilmente identificare i layer \textit{top} e \textit{bottom} abbiamo aggiunto,
a lato scheda, i testi TOP e BOT sui layer corrispondenti.\\
A questo punto la scheda si può considerare terminata e non è rimasto
altro da fare che generare i \textit{teardrops}, tramite un plugin dedicato, ed
esportare i file \textit{gerber} e \textit{drill} (che riportiamo negli allegati della
presente relazione).\\
A questo punto abbiamo importato i file \textit{gerber} in \emph{gerbview} per un
controllo finale. Grazie a quest'ultima ispezione abbiamo identificato
qualche piccolo errore che abbiamo prontamente corretto. Abbiamo infine
mandato tutti i file al Professore, che ha provveduto all'invio di
questi al produttore.

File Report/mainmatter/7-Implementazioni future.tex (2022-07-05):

\chapter{Implementazioni future}

Considerando i componenti mancanti, le funzionalità che vorremmo
implementare in un prossimo futuro sono le seguenti:

\begin{itemize}
\item Interfaccia utente attraverso il display \textit{OLED}
\item Sensing di tensione e corrente prodotti dal pannello
\item Struttura per pannello, motori e sensori
\item Interfaccia \textit{Python} via \textit{COM} port con visualizzazione valori, statistiche e controllo manuale motori
\end{itemize}

\noindent L'interfaccia utente nel display OLED mostrerà: tensione e
corrente del pannello, posizione del sole e posizione pannello (angolo di
Azimuth e angolo di Elevazione), orario e posizione geografica.

\begin{center}

\captionsetup{type=figure}
\captionof{figure}{Esempio di interfaccia utente su display OLED}
\end{center}

\noindent La struttura di supporto per il pannello servirà prima di tutto a
consentire al pannello di muoversi nei due gradi di libertà (rotazione
intorno all'asse Z e rotazione intorno all'asse Y) e poi per contenere
magnetometro ed accelerometro in modo che questi rilevino esattamente la
posizione del pannello (dovranno quindi essere fisicamente attaccati al
pannello e dovranno muoversi con esso).

\begin{center}



\captionsetup{type=figure}
\captionof{figure}{Esempio di struttura di supporto per pannello e motori di tipo servo\\
(Credits:\href{https://www.thingiverse.com/thing:53321}{\underline{https://www.thingiverse.com/thing:53321}})}
\end{center}

\noindent Per quanto riguarda l'interfaccia grafica per la connessione seriale via
USB, si pensava di sviluppare in \textit{GUI} (Graphical User Interface) in
linguaggio \textit{Python} che consentisse di controllare manualmente le
posizioni dei motori, di abilitare il tracking o il return to home e
che, attraverso l'uso di piccoli grafici, mostrasse delle semplici
statistiche sulla potenza e l'energia prodotte dal pannello
fotovoltaico.

\begin{center}

\captionsetup{type=figure}
\captionof{figure}{Esempio di GUI sviluppata in python}
\end{center}

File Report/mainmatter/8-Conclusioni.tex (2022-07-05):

\chapter{Conclusioni}

\hypertarget{resoconto-esperienza}{%
\section{\texorpdfstring{Resoconto esperienza
}{Resoconto esperienza }}\label{resoconto-esperienza}}

Il corso è stato formativo sotto tutti i punti di vista poiché abbiamo
potuto realizzare una scheda partendo da zero, cosa che negli altri
corsi non avevamo mai fatto. Per alcuni quindi è stata la prima PCB
progettata, perciò una tappa molto importante per il loro lavoro o
studio futuro. Inoltre il fatto di aver programmato il microcontrollore
con le poche basi di programmazione che avevamo dai corsi precedenti ci
ha permesso di imparare molto a livello firmware. Siccome il progetto
non è ancora completo, l'intenzione è quella di aggiungere man mano i
componenti mancanti al fine di avere la scheda più simile possibile a
quanto era stato programmato. Per concludere, i concetti imparati nel
modulo 1 del corso sono stati di fondamentale importanza per la
realizzazione della scheda, senza i quali sarebbe stato molto difficile
avere un'idea di come impostare il lavoro. L'obiettivo di progettare in
modo consono una scheda elettronica è dunque stato raggiunto.

\hypertarget{lezioni-imparate}{%
\section{Lezioni imparate}\label{Lezioni-imparate}}

\noindent Ragionando a posteriori su quanto abbiamo fatto, abbiamo stilato un
elenco di cosa avremmo potuto fare meglio e che cercheremo di applicare
nei progetti futuri:

\begin{itemize}
\item
  
  Il fanout del microcontrollore lo avremmo potuto fare esclusivamente
  con tracce da 0.2mm, senza ricorrere ad espansioni a 0.3mm, almeno per
  le tracce più corte. Questo avrebbe semplificato di non poco il
  routing di quella sezione;
  
\item
  
  Considerare fin da subito i return paths per i condensatori di
  decoupling. Nella realizzazione non abbiamo pensato a collegare alcuna
  traccia per il GND, perché ci siamo affidati ai poligoni di
  riempimento. Questo si è rivelato un problema, perché alla fine del
  progetto abbiamo riscontrato che molti riempimenti risultavano
  scollegati da GND e, soprattutto, che i percorsi effettivi delle linee
  di GND dei condensatori di bypass del microcontrollore sono risultati
  molto lunghi, il che rende quasi inutile il fatto di posizionarli
  vicini ai pin;
  
\item
  
  Controllare meglio il posizionamento dei refdes sul layer di
  silkscreen. Abbiamo realizzato solo a scheda prodotta che il refdes di
  C10 è stato posizionato sopra C14, rendendolo invisibile;
  
\item
  
  Controllare meglio i componenti scelti. Abbiamo infatti scelto di
  utilizzare un led rgb di un formato che in realtà si fatica a trovare sul
  mercato. Anche questo è stato scoperto solo in fase di assemblaggio.
  
\end{itemize}

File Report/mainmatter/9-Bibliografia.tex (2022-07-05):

\chapter{Bibliografia}

\begin{itemize}
  \item
  
  \href{https://github.com/thomasnonis/ppse-2021}{\underline{Repository
  progetto SALMO}}
\item
  
  \href{https://github.com/raspberrypi/pico-sdk}{\underline{Repository
  Pico SDK}}
  
\item
  
  \href{https://github.com/raspberrypi/pico-examples}{\underline{Repository
  Pico Examples}}
  
\item
  
  \href{https://github.com/raspberrypi/picotool}{\underline{Repository}
  \underline{Picotool}}
  
\item
  
  \href{https://raspberrypi.github.io/pico-sdk-doxygen/}{\underline{Documentazione
  Pico SDK}}
  
\item
  
  \href{https://datasheets.raspberrypi.com/pico/raspberry-pi-pico-c-sdk.pdf}{\underline{Raspberry
  Pi Pico C/C++ SDK}}
  
\item
  
  \href{https://datasheets.raspberrypi.com/rp2040/hardware-design-with-rp2040.pdf}{\underline{Hardware
  design with RP2040}}
  
\item
  
  \href{https://www.researchgate.net/publication/222131147_The_Astronomical_Almanac's_algorithm_for_approximate_solar_position_1950-2050}{\underline{The
  astronomical almanac's algorithm for approximate solar position}}
  
\item
  
  \href{https://www.nrel.gov/docs/fy08osti/34302.pdf}{\underline{Solar
  Position Algorithm for Solar Radiation Applications}}
  
\item
  
  \href{https://github.com/jrowberg/i2cdevlib/blob/master/STM32/HMC5883/HMC5883L.h}{\underline{Repository
  driver HMC5883L STM32}}
  
\item
  
  \href{https://github.com/Harinadha/STM32_MPU6050lib/blob/master/MPU6050.h}{\underline{Repository
  driver MPU6050 STM32}}
  
\item
  
  \href{https://github.com/kosma/minmea}{\underline{Repository NMEA
  parser minmea}}
  
\item
  
  \href{https://github.com/beshrkayali/pico_stepper}{\underline{Repository
  pico stepper driver}}
  
\item
  
  \href{https://swairlearn.bluecover.pt/nmea_analyser}{\underline{Tool
  online per analisi stringhe NMEA}}
  
\item
  
  \href{https://www.thingiverse.com/thing:53321}{\underline{Thingiverse
  dual axis solar tracker}}
  
\end{itemize}

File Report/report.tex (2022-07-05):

\documentclass{layout/tudelft-report}

%Compile faster without images
% \documentclass[draft]{layout/tudelft-report}

\usepackage{graphicx}
\usepackage{parskip}

%% Additional packages and commands
\setlist{itemsep=-2pt} % Reducing white space in lists slightly
\renewcommand{\deg}{\si{\degree}\xspace} % Use \deg easily, everywhere
\renewcommand{\figurename}{Figura}
\linespread{1.3}

%%%%%%%%%%%%%%%%%%%%%%%%%%%%%
%%%%% Begin of document %%%%%
%%%%%%%%%%%%%%%%%%%%%%%%%%%%%

\begin{document}

%% Roman page numbering
\frontmatter

%% Defining the main parameters
\title{Relazione finale - Modulo due}

\subtitle{\centering SALMO: \\ Solar Azimuth and eLevation Motorized lOcator}
\author{Lisa Santarossa 209386\\
        Thomas Nonis 209445\\
        Tommaso Canova 209270\\
        Simone Tollardo 209002\\
        Gabriele Berretta 209466
        }
        
\subject{Corso di Progettazione e Prototipazione di Sistemi Elettronici}
\date{Anno accademico 2021/22}
\affiliation{Università degli Studi di Trento}

\coverimage{layout/salmo.png} % Aspect ratio of 2:3 (portrait) recommended
\definecolor{title}{HTML}{ffffff} % Color for title

\makecover

\input{frontmatter/title-report}

\setcounter{tocdepth}{1}
\tableofcontents
%\listoffigures
%\listoftables

%% Arabic page numbering
\mainmatter

\input{mainmatter/1-Abstract}
\input{mainmatter/2-Analisi dello schematico}
\input{mainmatter/3-Analisi Layout PCB}
\input{mainmatter/4-Firmware}
\input{mainmatter/5-Assemblaggio della scheda}
\input{mainmatter/6-Testing della scheda}
\input{mainmatter/7-Implementazioni future}
\input{mainmatter/8-Conclusioni}
\input{mainmatter/9-Bibliografia}
\input{mainmatter/10-Allegati}

\end{document}

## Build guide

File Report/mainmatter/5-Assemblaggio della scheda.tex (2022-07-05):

\chapter{Assemblaggio della scheda}

Come già accennato in precedenza, una volta finita la fase di progetto della scheda, abbiamo inviato al Professore tutti i file relativi alla produzione (\textit{Gerber}, \textit{Drill} e \textit{BOM}), il quale ha poi provveduto ad inviare le PCB in produzione, ordinando anche uno stencil, e ad effettuare gli ordini per i componenti necessari.
Dopo circa due settimane dall’invio eravamo finalmente in possesso delle schede e della maggior parte dei componenti necessari, quindi abbiamo potuto cominciare l’assemblaggio, che è stato svolto sotto la supervisione del Professore presso il laboratorio di elettronica del FabLab. \\\
Prima di iniziare con la fase di assemblaggio, abbiamo effettuato un’ispezione visiva delle PCB sotto una lente per verificarne la correttezza; grazie a questa abbiamo identificato un solo problema: il marker sul layer \textit{silkscreen} per il pin 1 del microcontrollore non è stato stampato, probabilmente perché era troppo piccolo. \\
Abbiamo poi ispezionato anche lo \textit{stencil} per la pasta saldante ed abbiamo notato che il produttore non ha usato come riferimento il layer apposito, ma ha usato quello per la \textit{soldermask}. Per questo motivo sullo stencil erano presenti aperture anche in corrispondenza dei pad \textit{through-hole} del \textit{GPS} (che abbiamo provveduto a coprire con del nastro \textit{kapton}) e le aperture dei fiducials sono risultate più grandi del previsto, anche se questo non ha alcuna importanza per la realizzazione, quindi siamo passati allo step successivo. \\
Per iniziare l’assemblaggio abbiamo fissato una PCB con altre 4 utilizzando del nastro ed abbiamo allineato lo stencil fissandolo da un lato con altro nastro per poterlo alzare una volta finito, come in figura.

\begin{center}
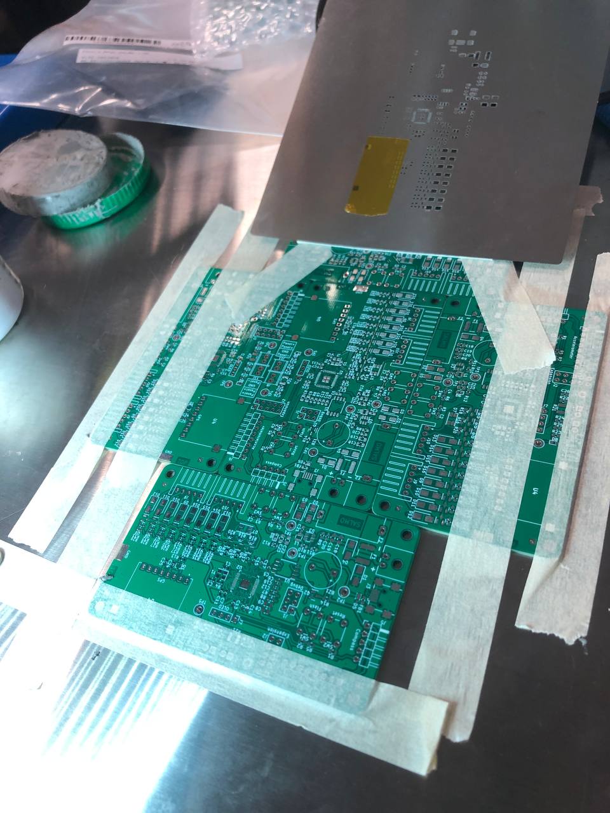
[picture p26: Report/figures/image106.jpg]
    
    \captionsetup{type=figure}
    \captionof{figure}{Il sistema utilizzato per fissare la scheda e lo stencil}
\end{center}

\noindent Abbiamo quindi depositato, con l’aiuto di una spatola, la pasta saldante, controllando di riempire ogni apertura con una quantità adeguata. Verificata la corretta applicazione abbiamo tolto la scheda dal supporto da noi creato ed abbiamo cominciato ad applicare i componenti \textit{SMD} con l’aiuto di pinzette di precisione e controllando continuamente il layout.

\begin{center}
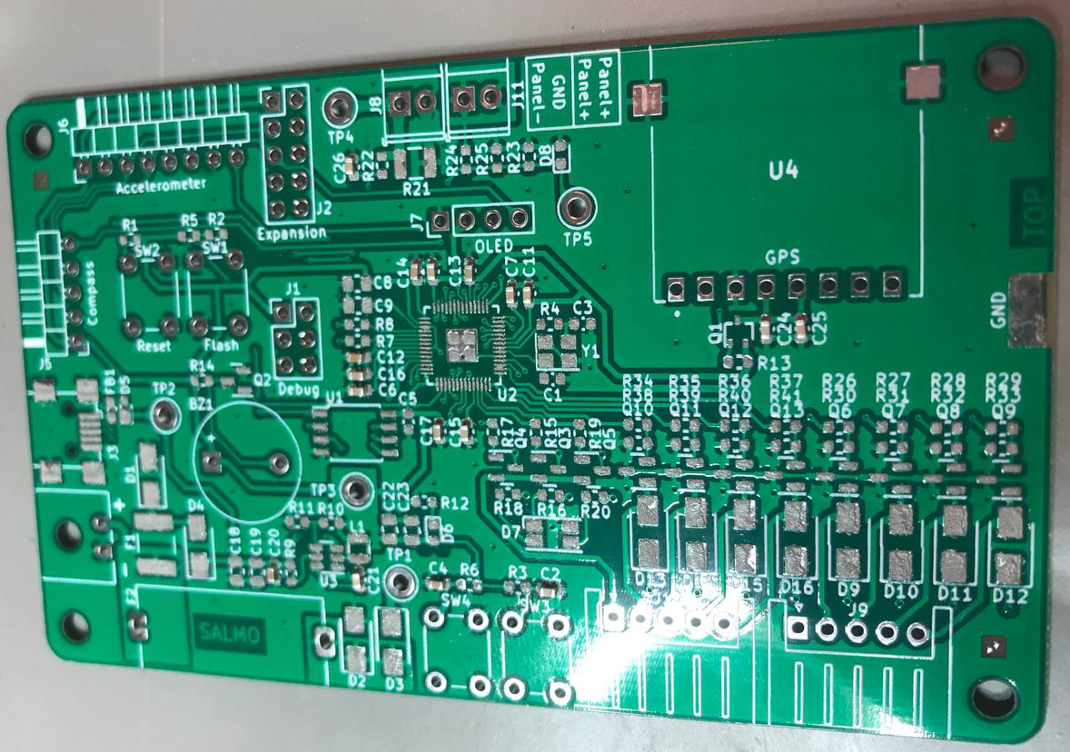
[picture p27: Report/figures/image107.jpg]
    
    \captionsetup{type=figure}
    \captionof{figure}{PCB con pasta applicata ed i primi componenti posizionati}
\end{center}

\noindent Per tenere traccia del progresso abbiamo usato estensivamente un utilissimo plugin per KiCad chiamato \textit{iBOM}, che permette di visualizzare il layout del PCB, associando ad ogni componente la sua posizione in una grafica molto intuitiva, e di contrassegnare ogni componente come piazzato.

\begin{center}
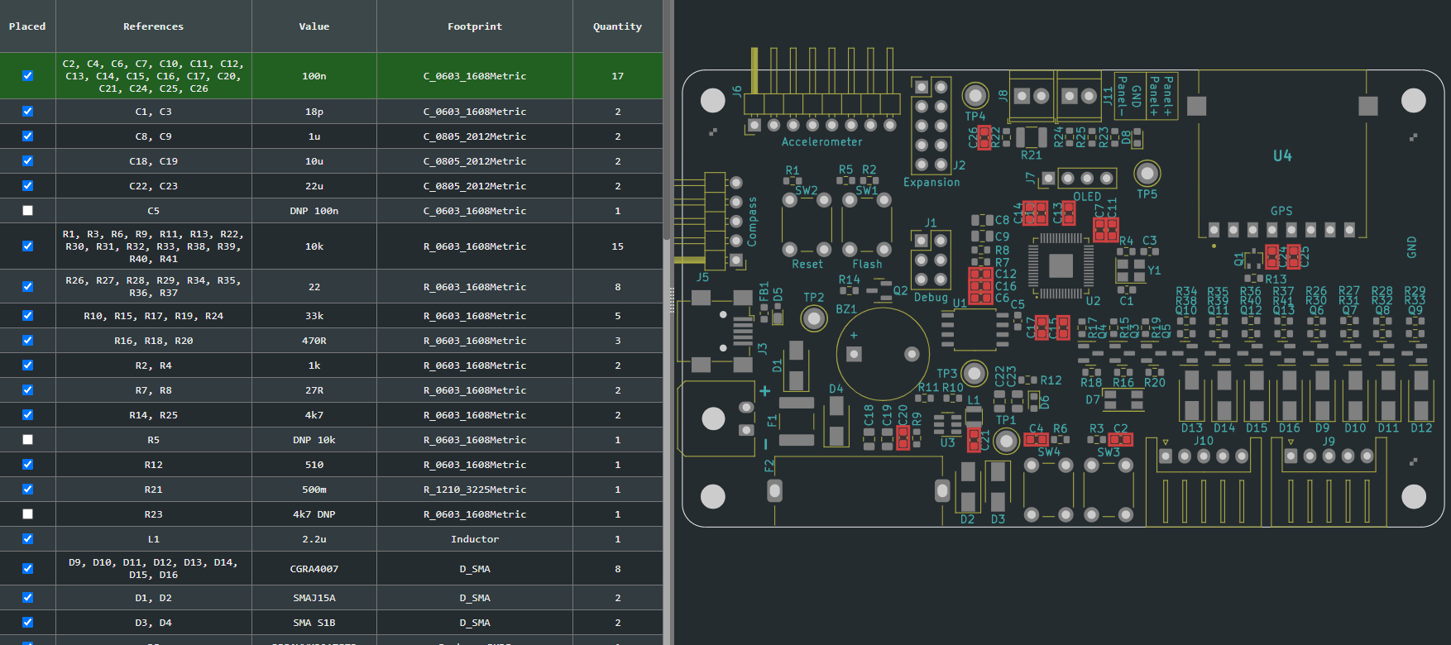
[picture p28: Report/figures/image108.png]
    
    \captionsetup{type=figure}
    \captionof{figure}{Interfaccia del plugin iBOM}
\end{center}

\noindent Alcuni dei componenti utilizzati presentavano un modello diverso da quello previsto in fase di progettazione a seconda delle disponibilità\textit{ in-house }del professore ma, essendo una scheda di prototipazione e non una scheda di produzione, sono risultati ugualmente adatti, senza alterarne il funzionamento. Infine, abbiamo posto la scheda su di una piastra elettrica riscaldante controllata per fare il reflow della pasta e saldare definitivamente i componenti \textit{SMD}. A questo punto abbiamo saldato manualmente, con un classico saldatore a stilo, i restanti componenti \textit{THT}, ovvero buzzer, pulsanti, portafusibile e connettori.

\noindent Abbiamo ripetuto questi passaggi per sei volte, realizzando così sei PCBA, uno per ogni membro del gruppo più uno per il professore.\\
Finito l’assemblaggio, ci siamo accorti che per una particolare scheda i pin del microcontrollore non sembravano 
essere fissati a dovere ed infatti testando la sua alimentazione abbiamo potuto constatare il surriscaldamento eccessivo 
del componente. Perciò per rimediare all’errore il microcontrollore è stato dissaldato, ma nel farlo, le tre piste che collegavano 
i rispettivi pin si sono alzate, non consentendo così l’utilizzo della scheda. Un altro errore è sorto durante la fase di testing, 
infatti, misurando il segnale di comando in input ai motori, ci siamo accorti che al transistor a canale N montato sulla scheda era 
stata assegnata la piedinatura scorretta. Pertanto, abbiamo dovuto dissaldare i transistor atti al pilotaggio dei motori per poi 
saldarli nuovamente nel verso corretto.\\
Come già anticipato non abbiamo potuto montare il led RGB a causa dell'errore nell'assegnamento del pinout e dell'errore nello schematico.

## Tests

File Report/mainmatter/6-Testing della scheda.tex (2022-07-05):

\chapter{Testing della scheda}

Terminato l’assemblaggio, siamo passati alla fase di testing, in cui abbiamo verificato il funzionamento delle schede in tutti i loro aspetti.
Anzitutto abbiamo provato ad alimentarle via USB per verificare che la regolazione di tensione fosse funzionante. Abbiamo sfruttato il led sulla rail dei 3.3V come indicatore principale, poi abbiamo effettuato una misura più accurata tramite multimetro, appurando che il dimensionamento è stato fatto in modo corretto. Infatti sul testpoint della rail abbiamo misurato $3.3V \pm 0.05V$. \\
Dopo aver appurato che l’alimentazione fosse funzionante abbiamo flashato il microcontrollore con il codice che abbiamo sviluppato in parallelo su una \textit{dev-board Raspberry Pi Pico} ed abbiamo verificato il corretto assemblaggio dei componenti. \\
Con un programma di prova abbiamo poi applicato un segnale di controllo ai motori e, analizzando l’uscita dello stadio con l’oscilloscopio, ci siamo accorti che in uscita non si aveva il segnale desiderato. Perciò prima abbiamo testato il segnale \textit{PWM} generato dal microcontrollore, il quale è risultato corretto. Poi siamo passati al test sui \textit{mosfet} di pilotaggio. Qui ci siamo accorti che il segnale era sbagliato, quindi abbiamo intuito che il problema fossero i transistor. Il professore ci ha poi aiutati a capire nel dettaglio il problema misurando la tensione ai capi del diodo di protezione tra drain e source del \textit{mosfet}. Risultando un cortocircuito tra drain e source abbiamo capito che quelli non erano realmente il drain e il source del \textit{mosfet}x e ci siamo accorti che, in fase di progetto, ai transistor a canale N montati sulla scheda era stata assegnata la piedinatura scorretta. Effettuando la misurazione di tensione tra i vari pin del transistor abbiamo capito quale fosse il gate ed abbiamo provveduto a dissaldare e risaldare i transistor nella posizione corretta. Dopo questa correzione il sistema di pilotaggio degli stepper è risultato funzionante.
I restanti componenti sono stati testati con diverse iterazioni del \textit{firmware} e sono risultatI perfettamente funzionanti. \\
Per concludere abbiamo misurato il consumo del prototipo all’avviamento dei motori e in modalità idle,  ricavando le seguenti misure:

\begin{itemize}
    \item consumo a motori attuati: $<1.2 W$;
    \item consumo in idle: $<0.25 W$;
\end{itemize}
I consumi totali risultano complessivamente bassi poiché, data l'elevata coppia statica dei motori, non è necessario alimentarli per tenerli in posizione fissa.

\begin{center}
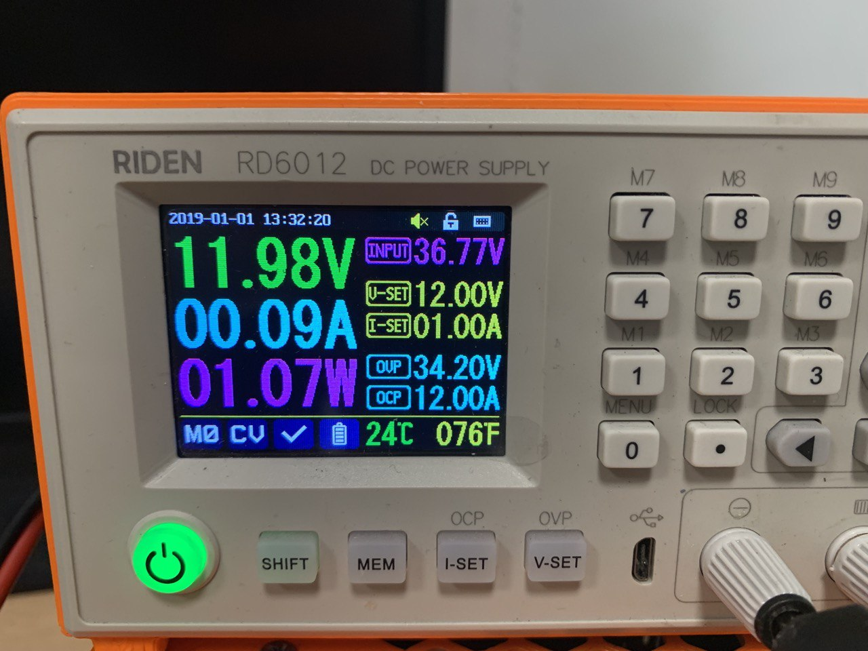
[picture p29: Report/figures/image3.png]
    
    \captionsetup{type=figure}
    \captionof{figure}{Consumi durante il movimento dei motori}
\end{center}

\begin{center}
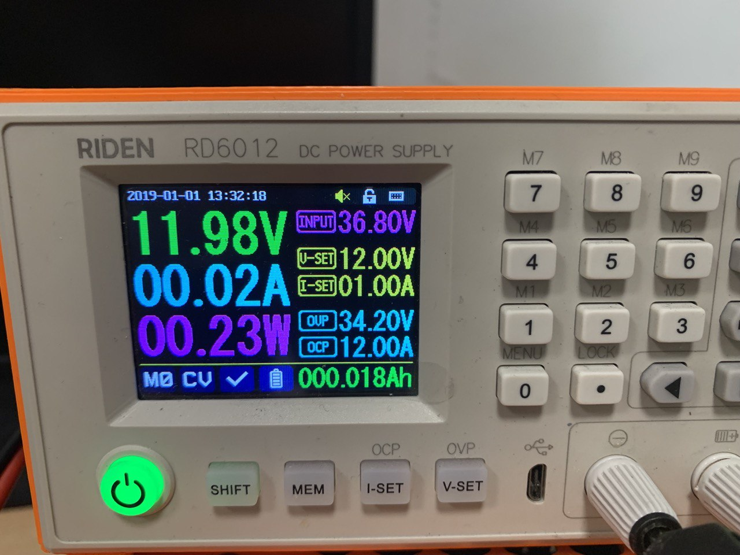
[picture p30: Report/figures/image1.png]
    
    \captionsetup{type=figure}
    \captionof{figure}{Consumi durante lo stato di idle}
\end{center}

\begin{center}
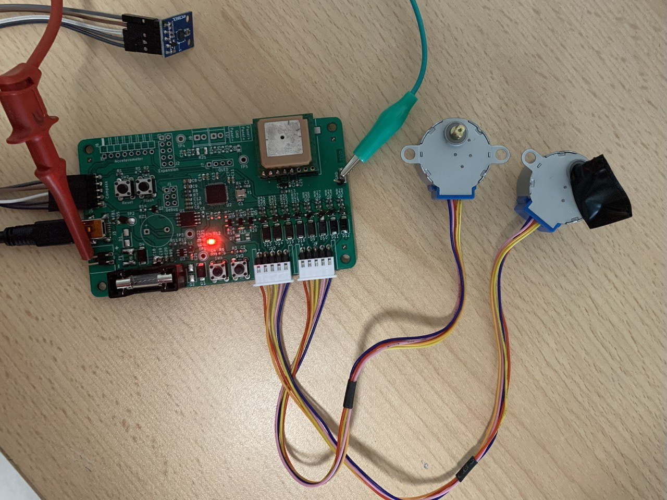
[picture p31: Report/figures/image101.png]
    
    \captionsetup{type=figure}
    \captionof{figure}{La scheda in fase di testing}
\end{center}

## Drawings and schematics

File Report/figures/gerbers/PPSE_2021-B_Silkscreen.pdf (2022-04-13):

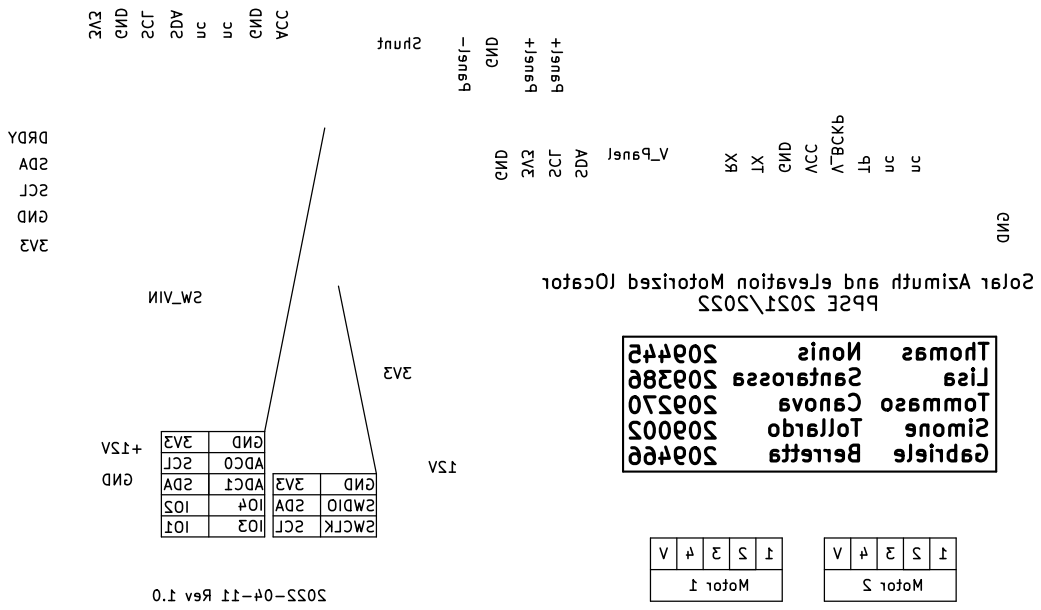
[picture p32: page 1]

2 SDA Shunt GND Panel- GNDGND

4 3 Nonis Santarossa Canova Tollardo Berretta 3V3 nc

4 SCL TXnc nc GND

SWCLK ACC GND Panel+

SCL SDA 3V3 SDA Thomas Lisa Tommaso Simone Gabriele

Solar Azimuth and eLevation Motorized lOcator PPSE 2021/2022

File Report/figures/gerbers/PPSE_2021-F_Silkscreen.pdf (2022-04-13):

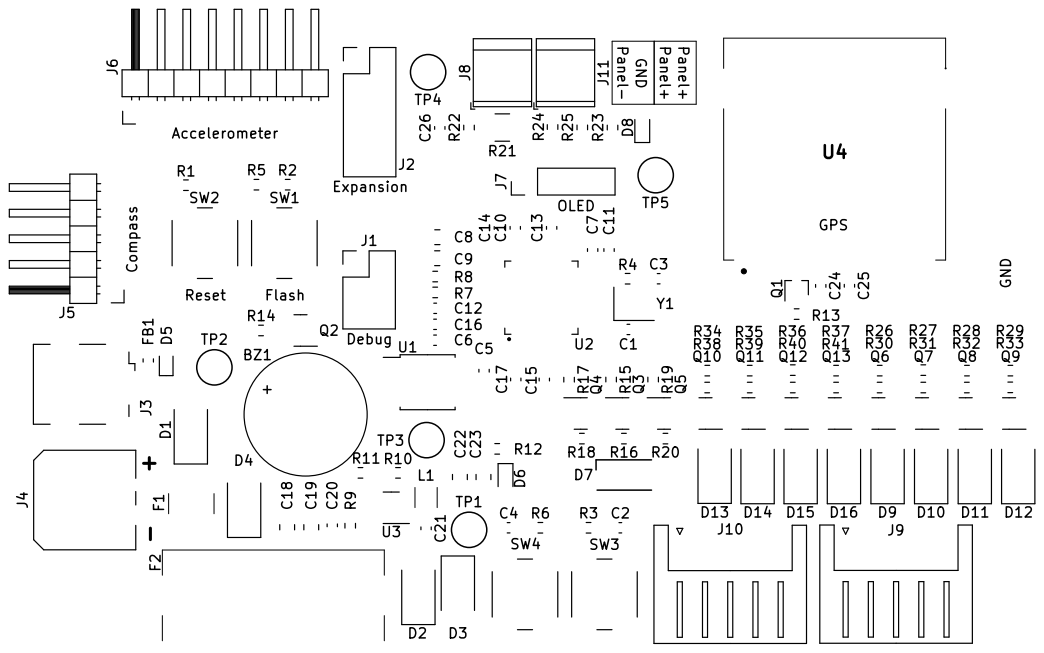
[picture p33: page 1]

- Accelerometer GPS OLED Compass GND GND

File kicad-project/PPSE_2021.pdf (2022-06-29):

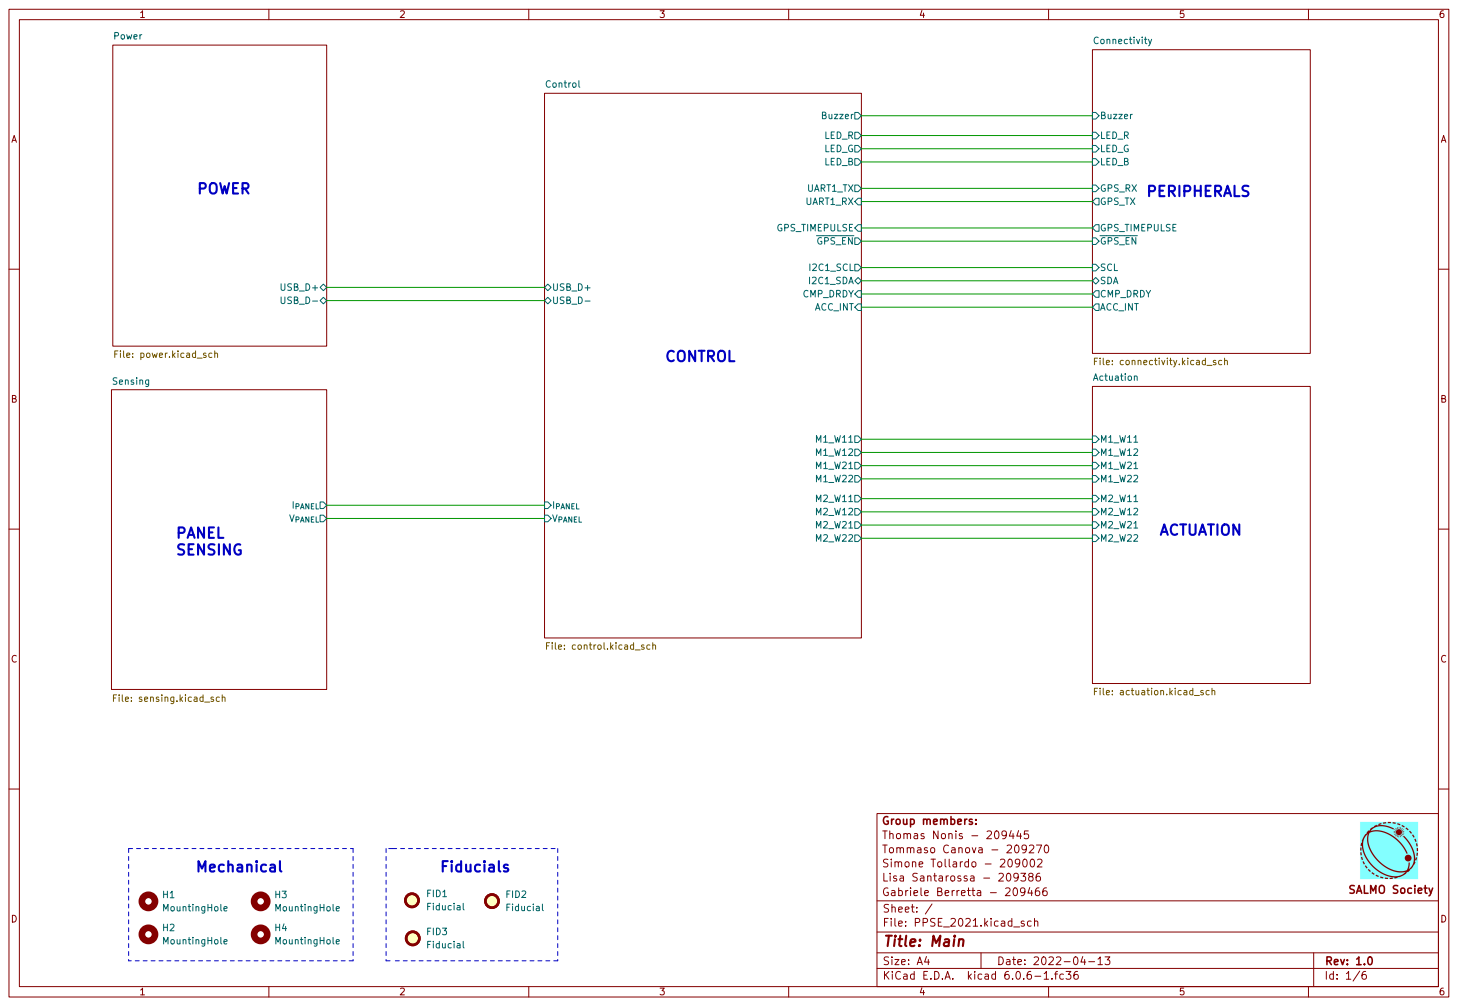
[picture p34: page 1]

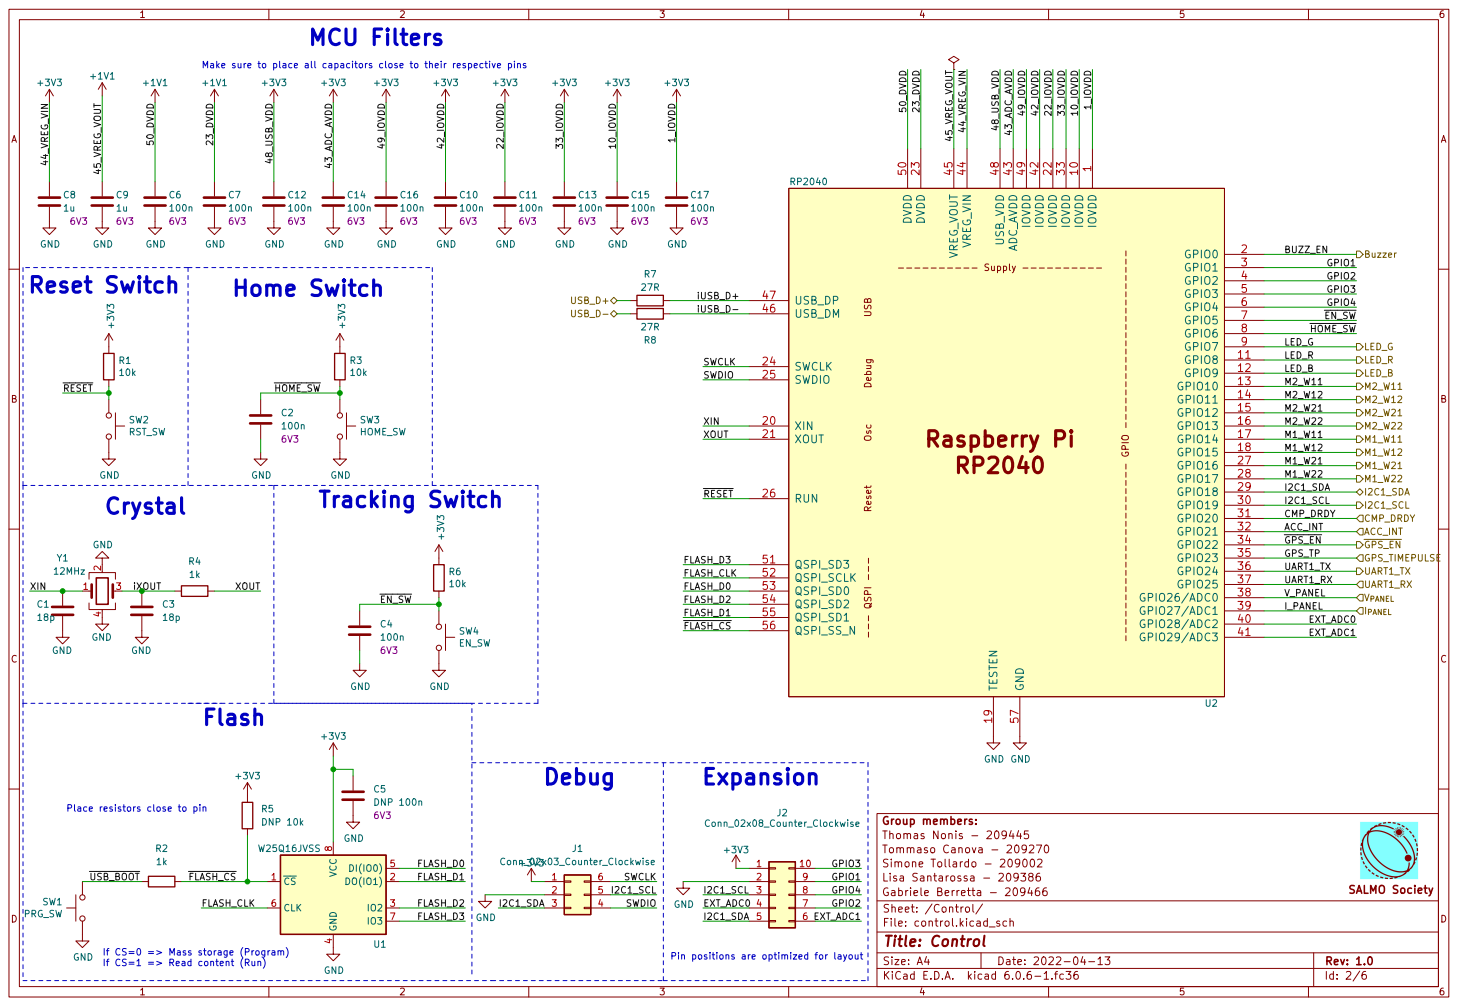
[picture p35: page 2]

Make sure to place all capacitors close to their respective pins

1 IOVDD 10 GPIO8 11 GPIO9 12 GPIO10 13 GPIO11 14 GPIO12 15 GPIO13 16 GPIO14 17 GPIO15 18 TESTEN 19 GPIO0 2 XIN 20 XOUT 21 IOVDD 22 DVDD 23 SWCLK 24 SWDIO 25 RUN 26 GPIO16 27 GPIO17 28 GPIO18 29 GPIO1 3 GPIO19 30 GPIO20 31 GPIO21 32 IOVDD 33 GPIO22 34 GPIO23 35 GPIO24 36 GPIO25 37 GPIO26/ADC0 38 GPIO27/ADC1 39 GPIO2 4 GPIO28/ADC2 40 GPIO29/ADC3 41 IOVDD 42 ADC_AVDD 43 VREG_VIN 44 VREG_VOUT 45

Place resistors close to pin
J2 Conn_02x08_Counter_Clockwise GND GND

Lisa Santarossa - 209386 Group members: Gabriele Berretta - 209466

If CS=0 => Mass storage (Program)
If CS=1 => Read content (Run)

Pin positions are optimized for layout

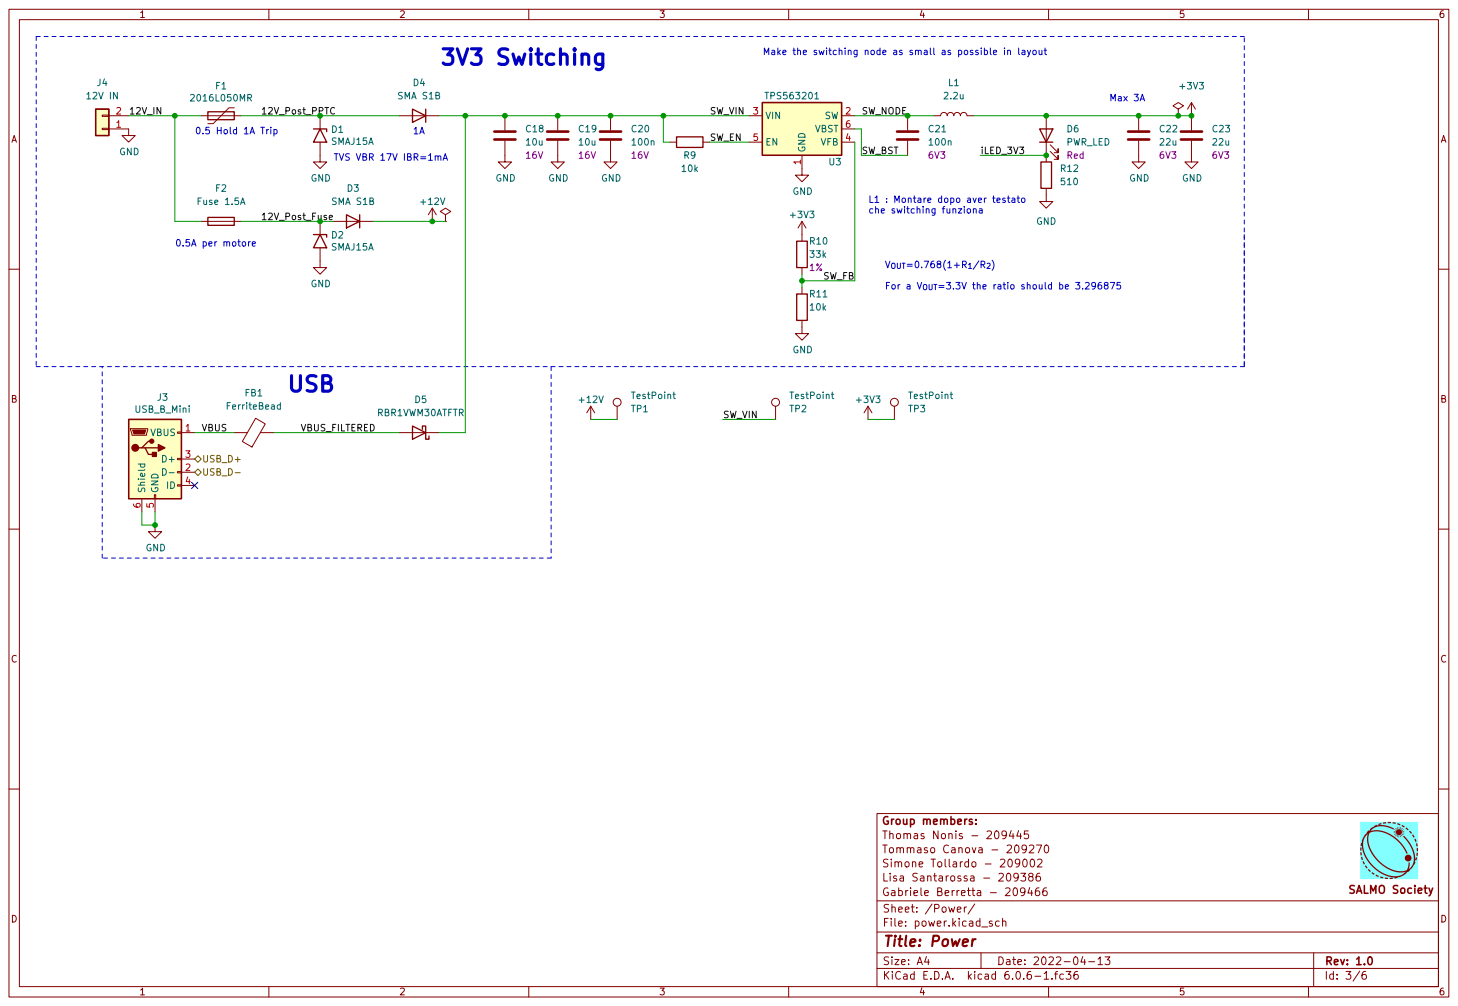
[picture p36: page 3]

Make the switching node as small as possible in layout TVS VBR 17V IBR=1mA 3V3 Switching

1 SW 2 VIN 3 VFB 4 EN 5 VBST 6 U3 TPS563201 F2 Fuse 1.5A

L1 : Montare dopo aver testato
che switching funziona

For a V_{OUT}=3.3V the ratio should be 3.296875

Lisa Santarossa - 209386 Group members: Gabriele Berretta - 209466

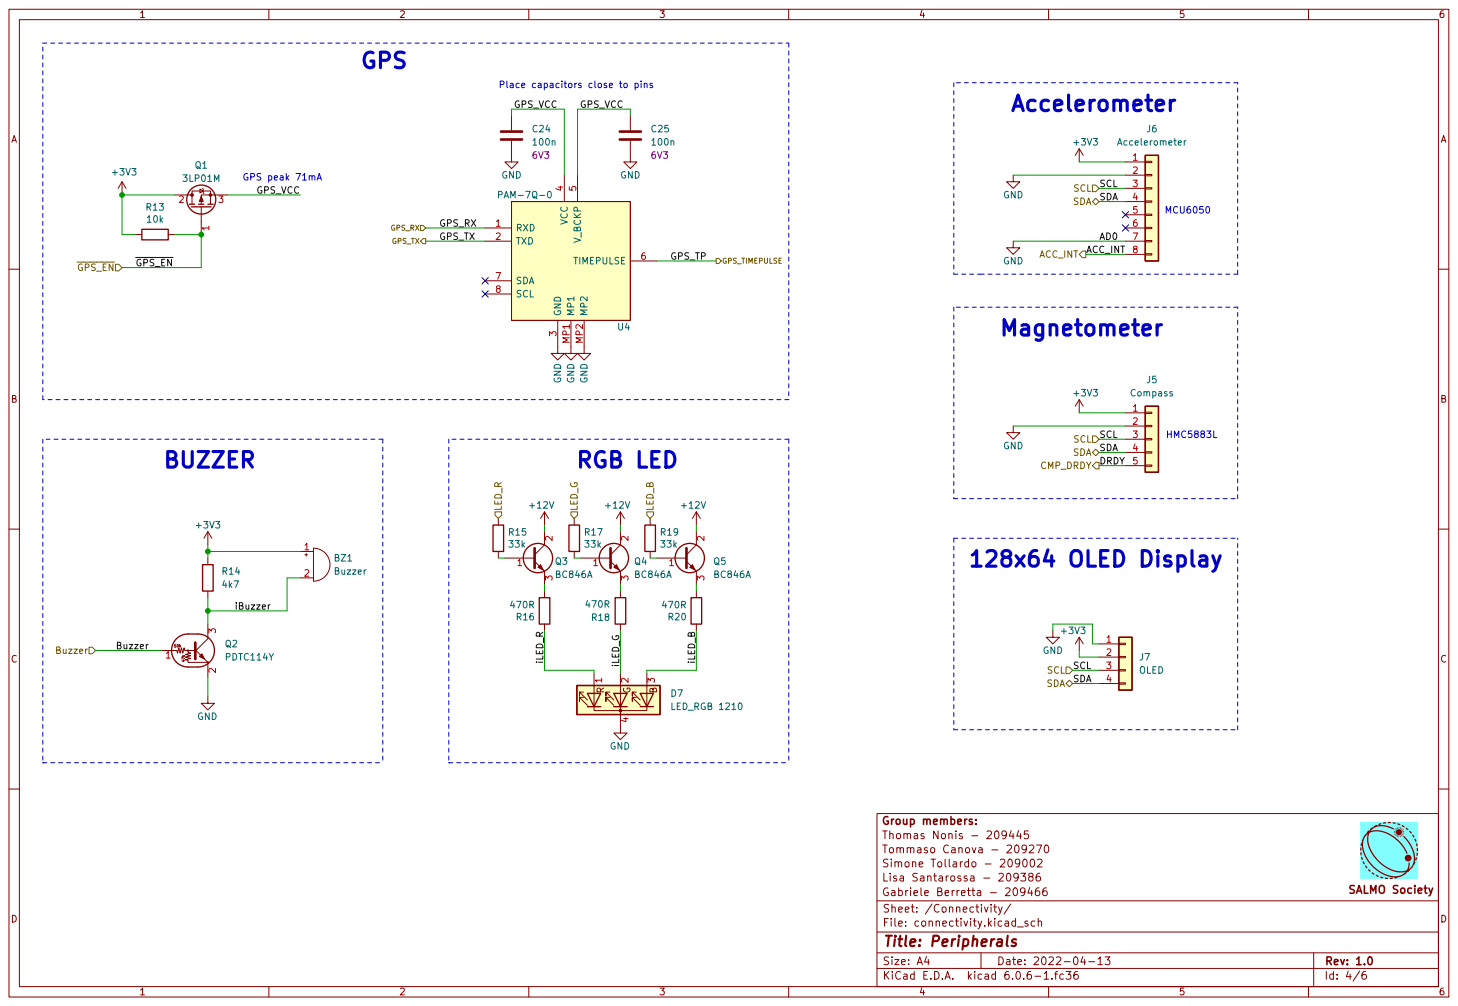
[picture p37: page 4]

5 TIMEPULSE 6 SDA 7 SCL 8 MP1 MP1 MP2 MP2U4 PAM-7Q-0 GND GND GND GND

Lisa Santarossa - 209386 Group members: Gabriele Berretta - 209466
SALMO Society Thomas Nonis - 209445 Tommaso Canova - 209270 Simone Tollardo - 209002

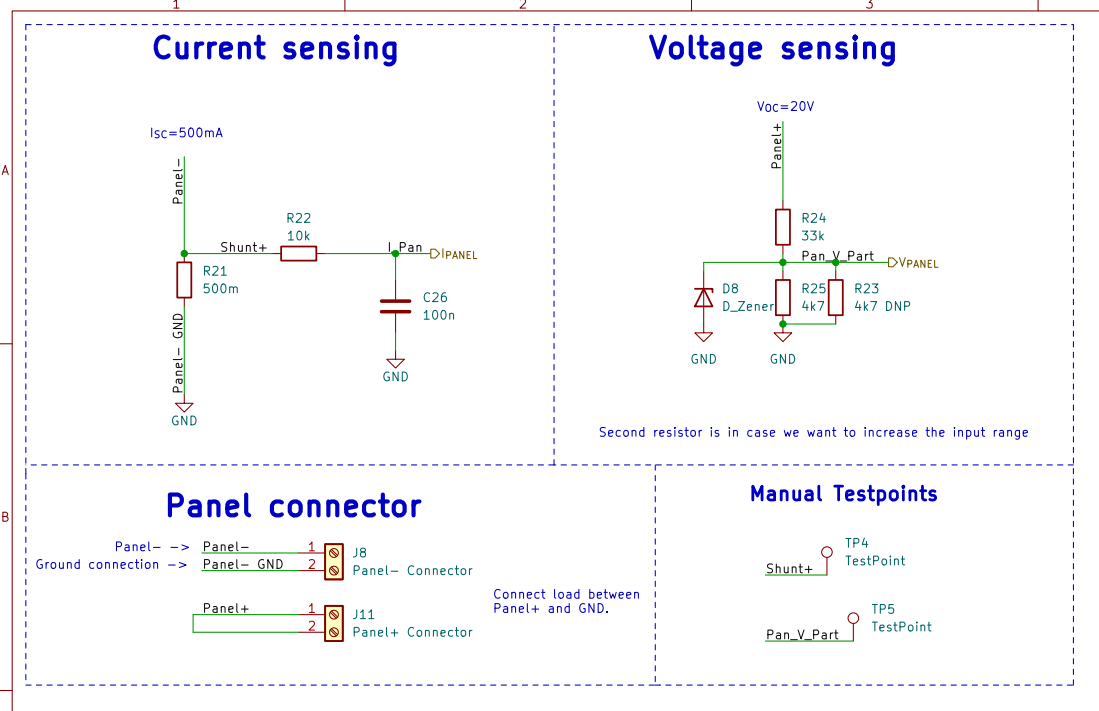
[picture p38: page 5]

Second resistor is in case we want to increase the input range

Connect load between Panel+ and GND.

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

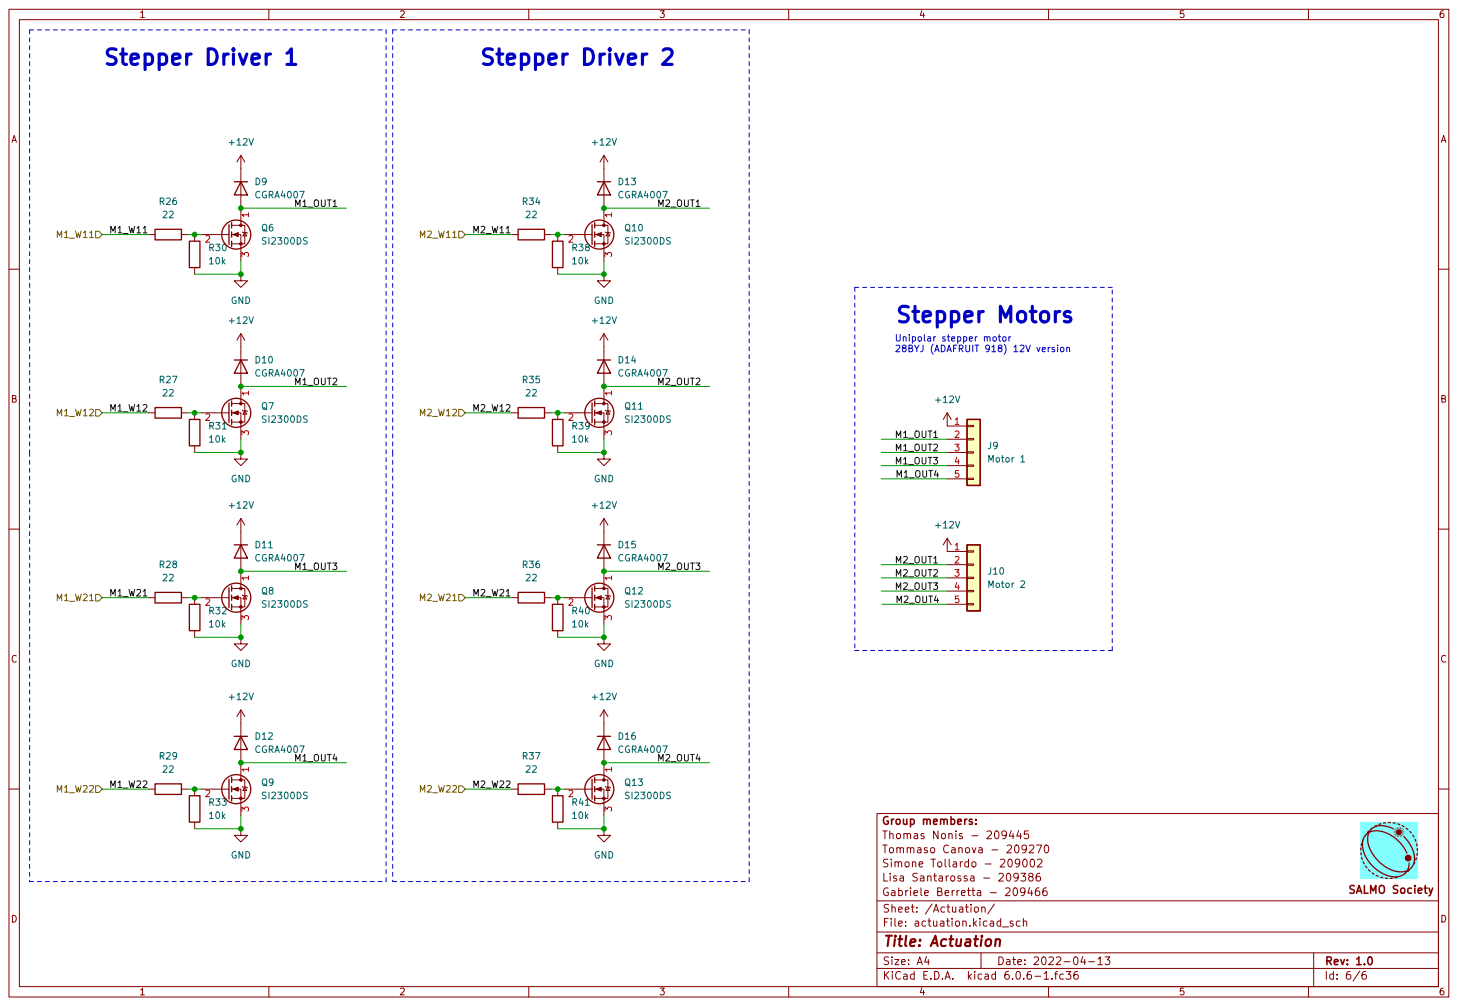
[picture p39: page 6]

Lisa Santarossa - 209386 Group members: Gabriele Berretta - 209466 GND

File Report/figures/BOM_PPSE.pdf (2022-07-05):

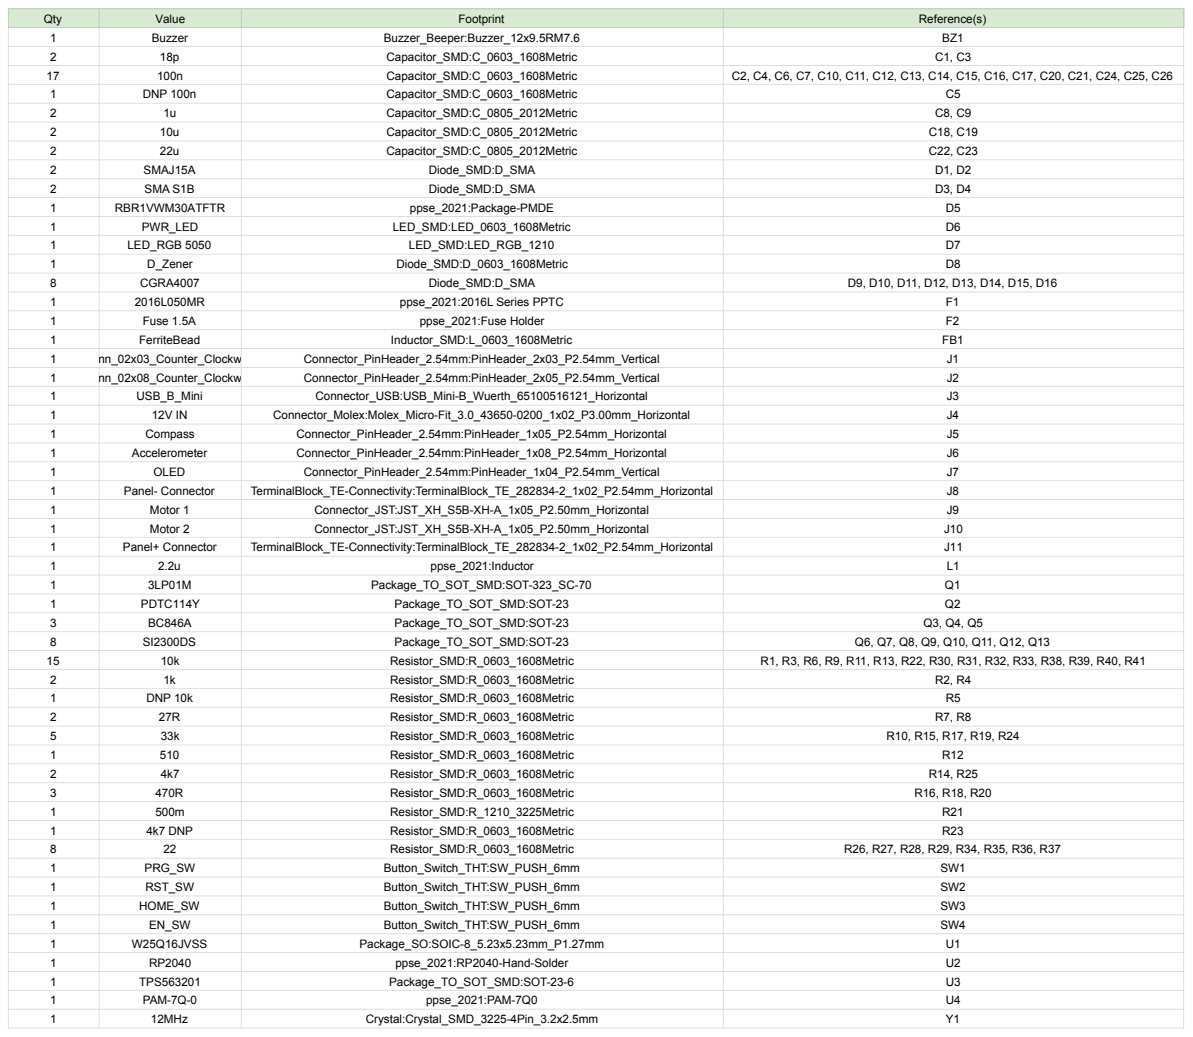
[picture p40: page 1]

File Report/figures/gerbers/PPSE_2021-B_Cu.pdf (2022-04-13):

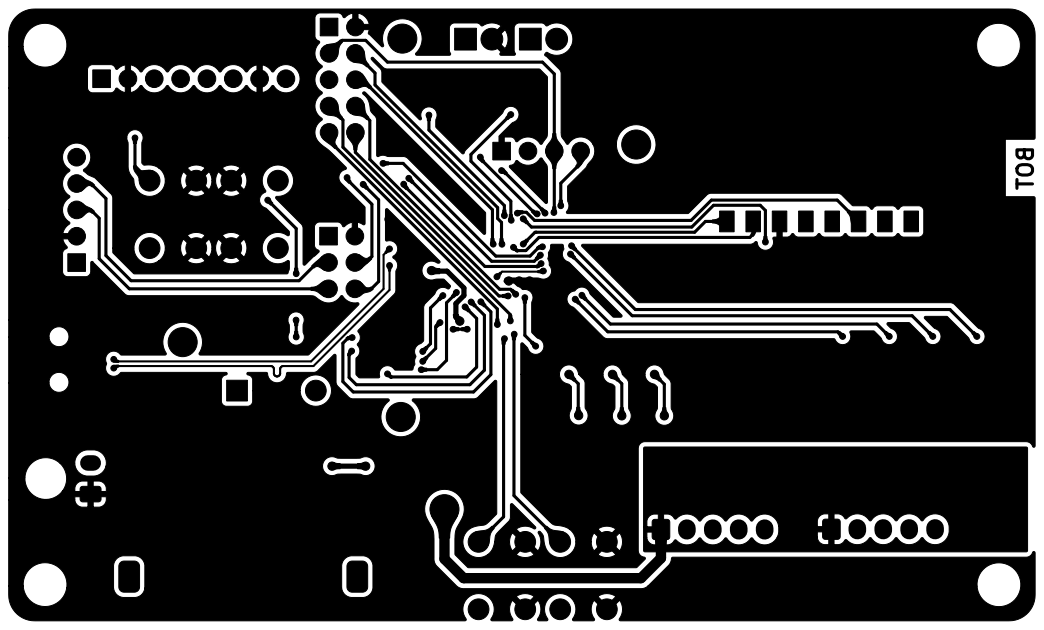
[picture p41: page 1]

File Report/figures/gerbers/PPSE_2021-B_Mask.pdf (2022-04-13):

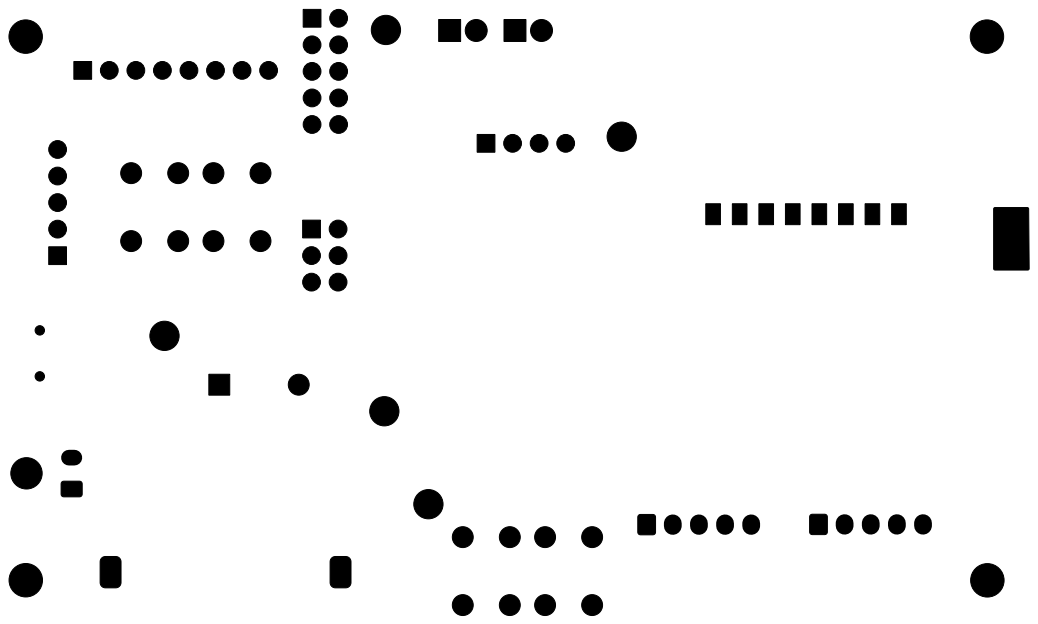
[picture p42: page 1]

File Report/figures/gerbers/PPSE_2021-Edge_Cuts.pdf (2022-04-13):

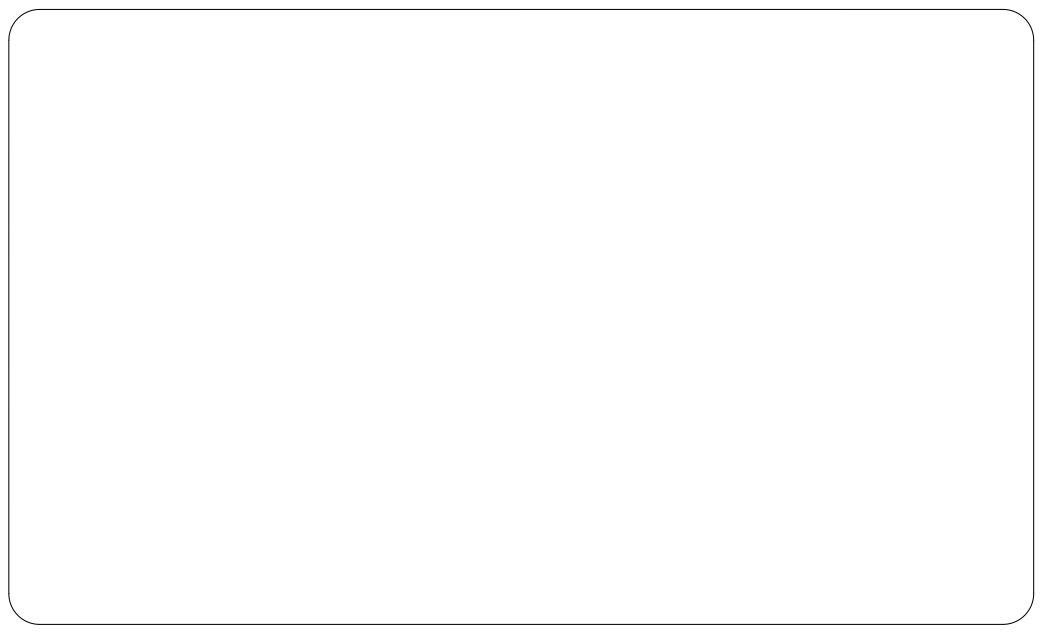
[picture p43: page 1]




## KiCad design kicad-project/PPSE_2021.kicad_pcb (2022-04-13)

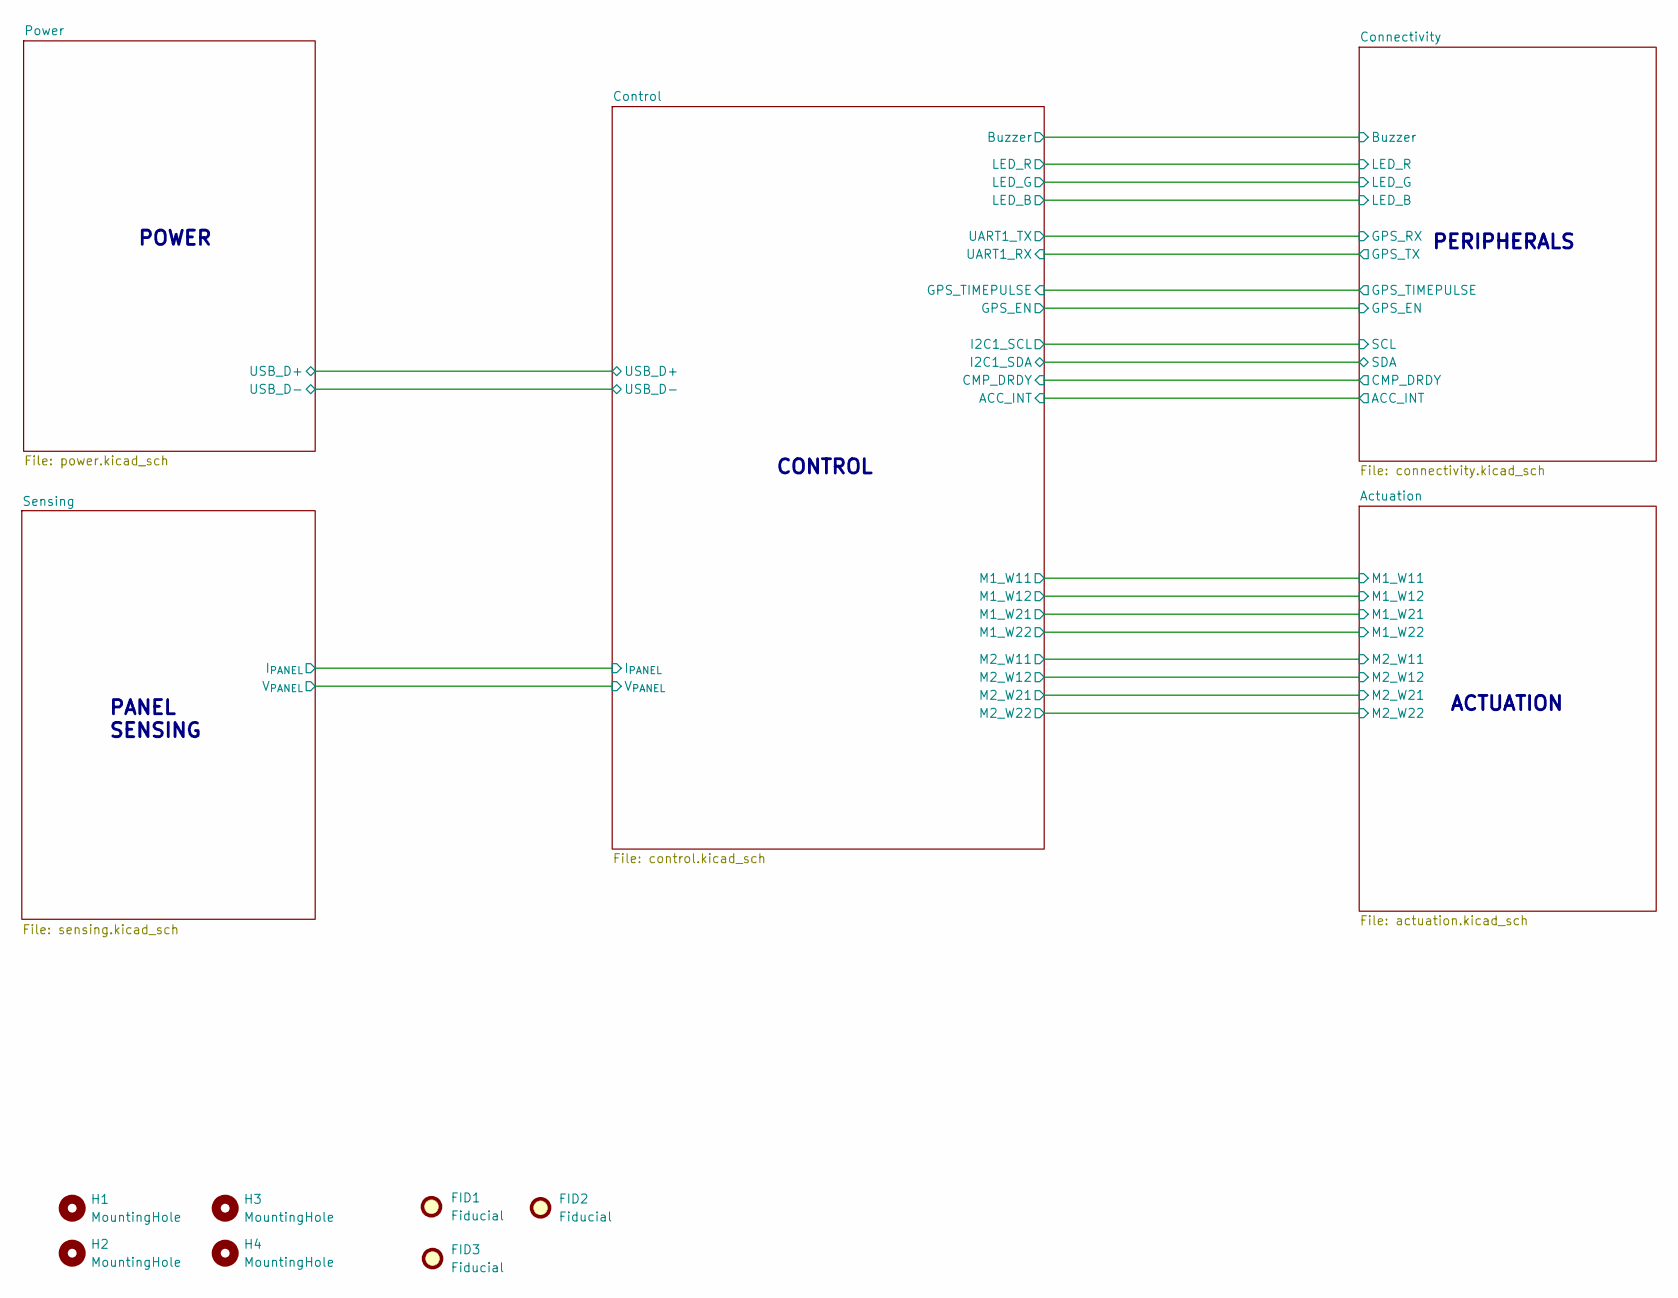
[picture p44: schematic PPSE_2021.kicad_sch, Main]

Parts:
FID1, FID2, FID3: Fiducial; Fiducial-ppse
H1, H2, H3, H4: MountingHole; MountingHole_3.2mm_M3

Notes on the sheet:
PERIPHERALS
PANEL SENSING
CONTROL
ACTUATION
POWER

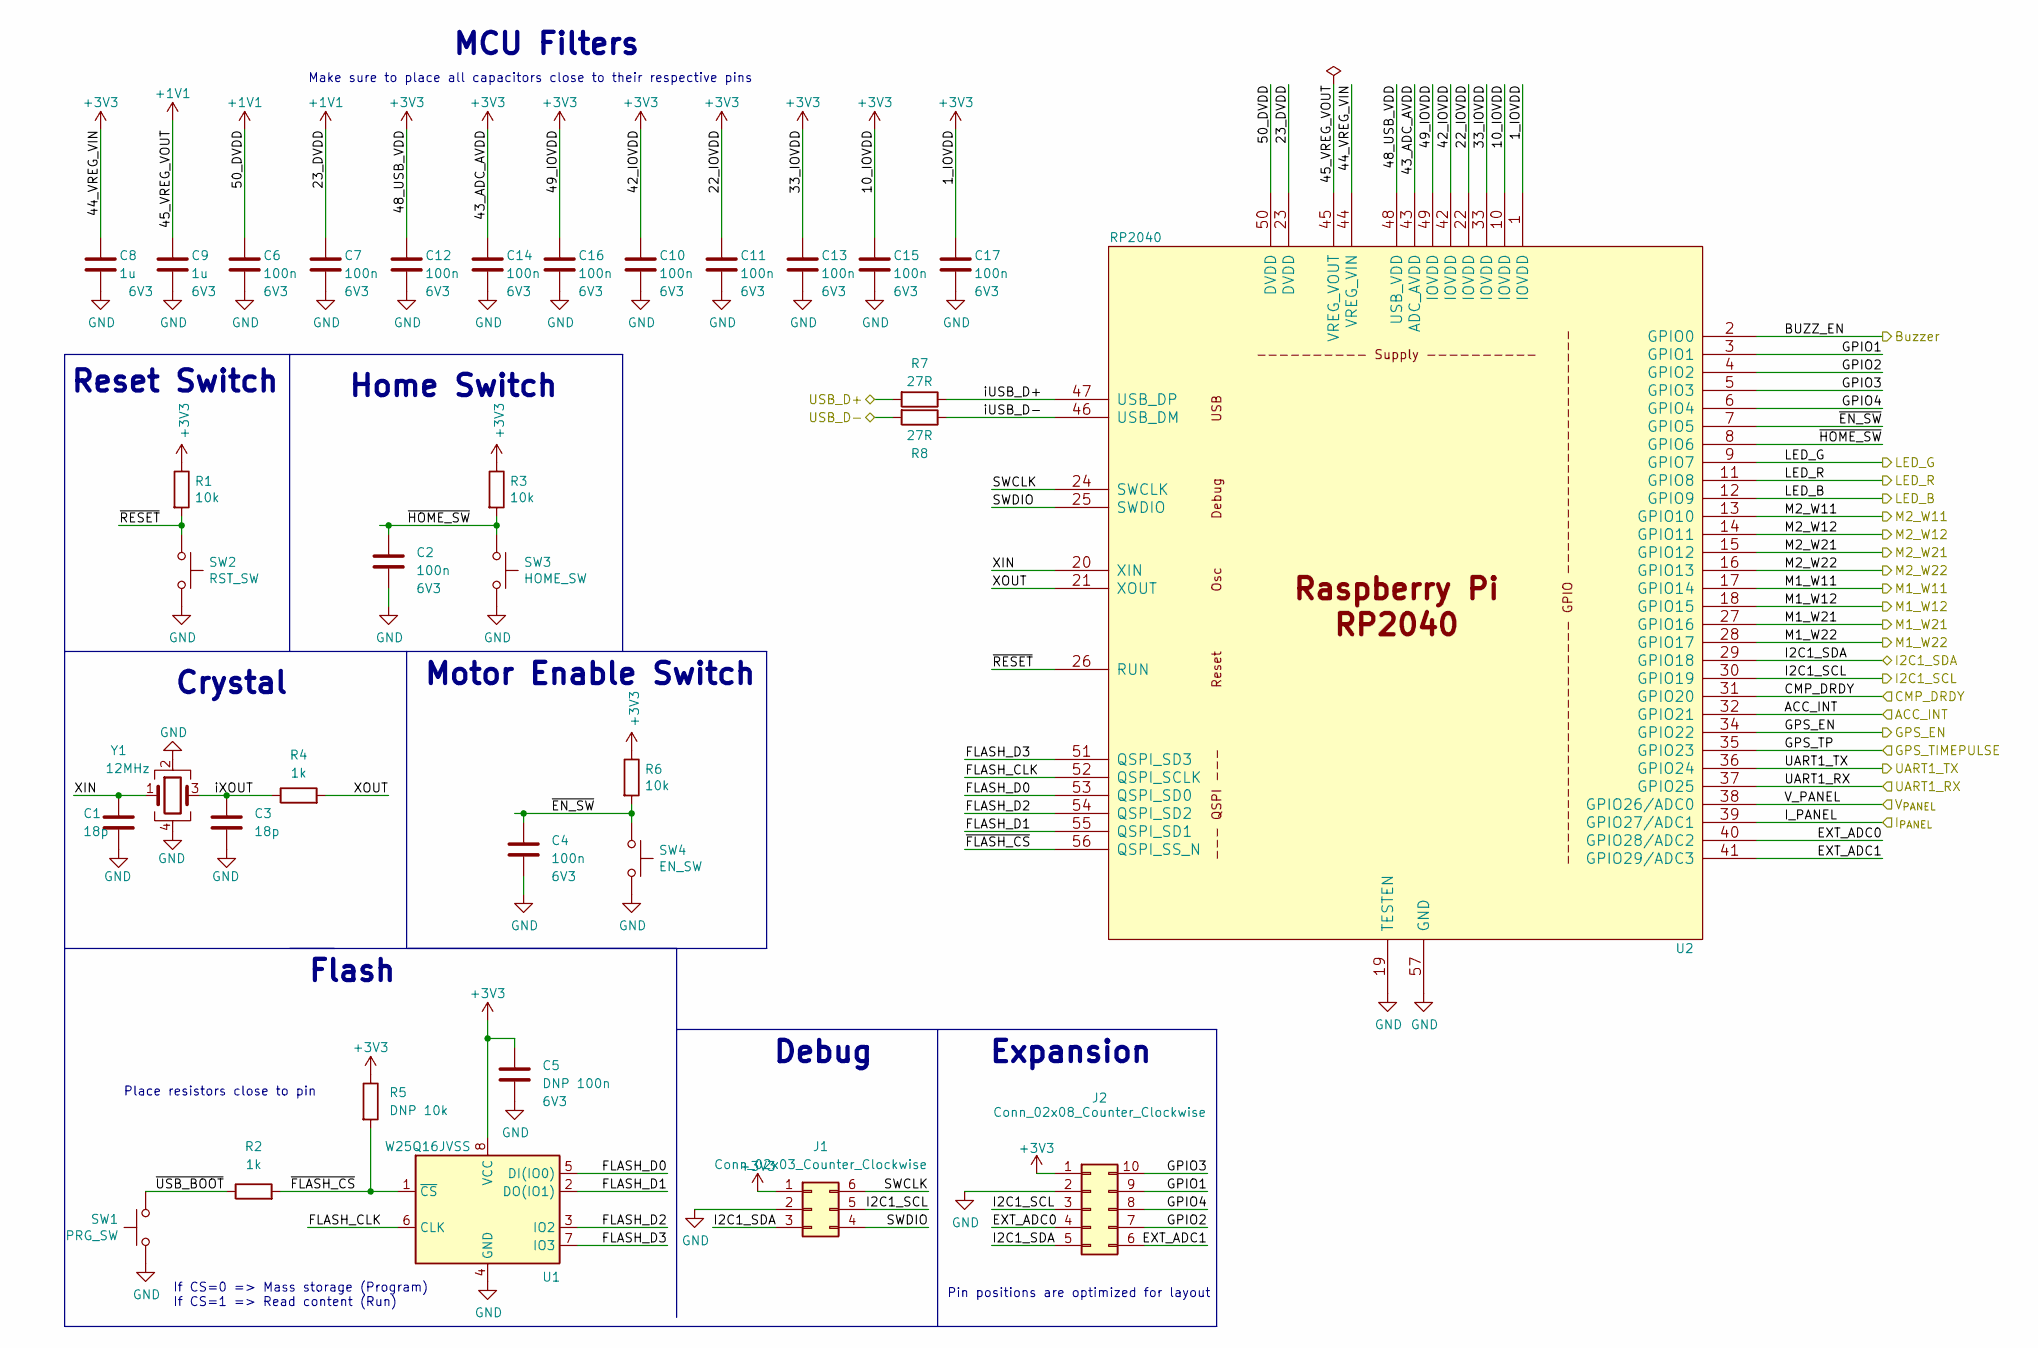
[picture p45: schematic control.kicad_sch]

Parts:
C1, C3: 18p; C_0603_1608Metric
C2, C4, C6, C7, C10, C11, C12, C13, C14, C15, C16, C17: 100n; C_0603_1608Metric; Voltage 6V3
C5: DNP 100n; C_0603_1608Metric; Voltage 6V3
C8, C9: 1u; C_0805_2012Metric; Voltage 6V3
J1: Conn_02x03_Counter_Clockwise; PinHeader_2x03_P2.54mm_Vertical
J2: Conn_02x08_Counter_Clockwise; PinHeader_2x05_P2.54mm_Vertical
R1, R3, R6: 10k; R_0603_1608Metric
R2, R4: 1k; R_0603_1608Metric
R5: DNP 10k; R_0603_1608Metric
R7, R8: 27R; R_0603_1608Metric
SW1: PRG_SW; SW_PUSH_6mm
SW2: RST_SW; SW_PUSH_6mm
SW3: HOME_SW; SW_PUSH_6mm
SW4: EN_SW; SW_PUSH_6mm
U1: W25Q16JVSS; SOIC-8_5.23x5.23mm_P1.27mm
U2: RP2040; RP2040-Hand-Solder
Y1: 12MHz; Crystal_SMD_3225-4Pin_3.2x2.5mm

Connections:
+1V1: C6.1, C7.1, C9.1, U2.23 (DVDD), U2.45 (VREG_VOUT), U2.50 (DVDD)
+3V3: C5.1, C8.1, C10.1, C11.1, C12.1, C13.1, C14.1, C15.1, C16.1, C17.1, J1.1, J2.1, R1.1, R3.1, R5.1, R6.1, U1.8 (VCC), U2.1 (IOVDD), U2.10 (IOVDD), U2.22 (IOVDD), U2.33 (IOVDD), U2.42 (IOVDD), U2.43 (ADC_AVDD), U2.44 (VREG_VIN), U2.48 (USB_VDD), U2.49 (IOVDD); also elsewhere on the board
/Actuation/M1_W11: U2.17 (GPIO14); also elsewhere on the board
/Actuation/M1_W12: U2.18 (GPIO15); also elsewhere on the board
/Actuation/M1_W21: U2.27 (GPIO16); also elsewhere on the board
/Actuation/M1_W22: U2.28 (GPIO17); also elsewhere on the board
/Actuation/M2_W11: U2.13 (GPIO10); also elsewhere on the board
/Actuation/M2_W12: U2.14 (GPIO11); also elsewhere on the board
/Actuation/M2_W21: U2.15 (GPIO12); also elsewhere on the board
/Actuation/M2_W22: U2.16 (GPIO13); also elsewhere on the board
/Connectivity/ACC_INT: U2.32 (GPIO21); also elsewhere on the board
/Connectivity/Buzzer: U2.2 (GPIO0); also elsewhere on the board
/Connectivity/DRDY: U2.31 (GPIO20); also elsewhere on the board
/Connectivity/GPS_EN: U2.34 (GPIO22); also elsewhere on the board
/Connectivity/GPS_RX: U2.36 (GPIO24); also elsewhere on the board
/Connectivity/GPS_TP: U2.35 (GPIO23); also elsewhere on the board
/Connectivity/GPS_TX: U2.37 (GPIO25); also elsewhere on the board
/Connectivity/SCL: J1.5, J2.3, U2.30 (GPIO19); also elsewhere on the board
/Connectivity/SDA: J1.3, J2.5, U2.29 (GPIO18); also elsewhere on the board
/Control/EXT_ADC0: J2.4, U2.40 (GPIO28/ADC2)
/Control/EXT_ADC1: J2.6, U2.41 (GPIO29/ADC3)
/Control/FLASH_CLK: U1.6 (CLK), U2.52 (QSPI_SCLK)
/Control/FLASH_D0: U1.5 (DI(IO0)), U2.53 (QSPI_SD0)
/Control/FLASH_D1: U1.2 (DO(IO1)), U2.55 (QSPI_SD1)
/Control/FLASH_D2: U1.3 (IO2), U2.54 (QSPI_SD2)
/Control/FLASH_D3: U1.7 (IO3), U2.51 (QSPI_SD3)
/Control/GPIO1: J2.9, U2.3 (GPIO1)
/Control/GPIO2: J2.7, U2.4 (GPIO2)
/Control/GPIO3: J2.10, U2.5 (GPIO3)
/Control/GPIO4: J2.8, U2.6 (GPIO4)
/Control/I_PANEL: U2.39 (GPIO27/ADC1); also elsewhere on the board
/Control/LED_B: U2.12 (GPIO9); also elsewhere on the board
/Control/LED_G: U2.9 (GPIO7); also elsewhere on the board
/Control/LED_R: U2.11 (GPIO8); also elsewhere on the board
/Control/SWCLK: J1.6, U2.24 (SWCLK)
/Control/SWDIO: J1.4, U2.25 (SWDIO)
/Control/USB_D+: R7.2; also elsewhere on the board
/Control/USB_D-: R8.2; also elsewhere on the board
/Control/V_PANEL: U2.38 (GPIO26/ADC0); also elsewhere on the board
/Control/XIN: C1.1, U2.20 (XIN), Y1.1
/Control/XOUT: R4.2, U2.21 (XOUT)
/Control/iUSB_D+: R7.1, U2.47 (USB_DP)
/Control/iUSB_D-: R8.1, U2.46 (USB_DM)
/Control/iXOUT: C3.1, R4.1, Y1.3
/Control/~EN_SW: C4.1, R6.2, SW4.1, U2.7 (GPIO5)
/Control/~FLASH_CS: R2.2, R5.2, U1.1 (~CS), U2.56 (QSPI_SS_N)
/Control/~HOME_SW: C2.1, R3.2, SW3.1, U2.8 (GPIO6)
/Control/~RESET: R1.2, SW2.1, U2.26 (RUN)
/Control/~USB_BOOT: R2.1, SW1.1
GND: C1.2, C2.2, C3.2, C4.2, C5.2, C6.2, C7.2, C8.2, C9.2, C10.2, C11.2, C12.2, C13.2, C14.2, C15.2, C16.2, C17.2, J1.2, J2.2, SW1.2, SW2.2, SW3.2, SW4.2, U1.4 (GND), U2.19 (TESTEN), U2.57 (GND), Y1.2, Y1.4; also elsewhere on the board

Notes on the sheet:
Expansion
Place resistors close to pin
MCU Filters
Home Switch
Make sure to place all capacitors close to their respective pins
Motor Enable Switch
Pin positions are optimized for layout
Flash
Debug
Reset Switch
If CS=0 => Mass storage (Program) If CS=1 => Read content (Run)
Crystal

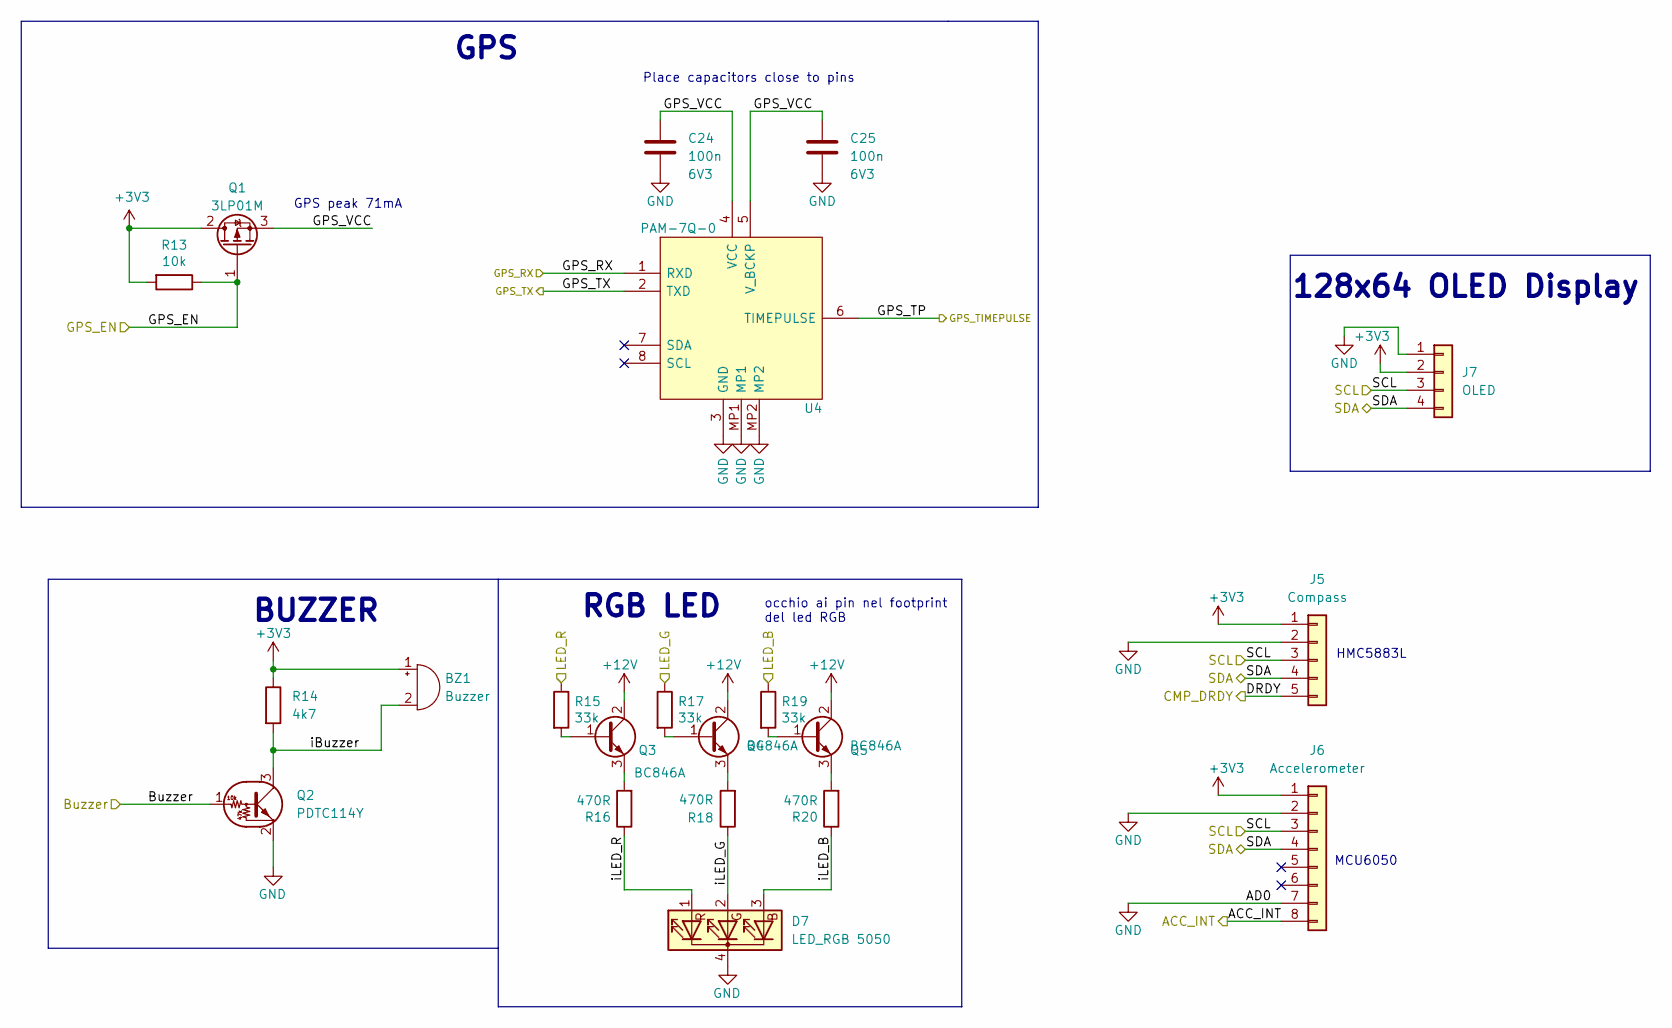
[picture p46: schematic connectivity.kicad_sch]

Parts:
BZ1: Buzzer; Buzzer_12x9.5RM7.6
C24, C25: 100n; C_0603_1608Metric; Voltage 6V3
D7: LED_RGB 5050; LED_RGB_1210
J5: Compass; PinHeader_1x05_P2.54mm_Horizontal
J6: Accelerometer; PinHeader_1x08_P2.54mm_Horizontal
J7: OLED; PinHeader_1x04_P2.54mm_Vertical
Q1: 3LP01M; SOT-323_SC-70
Q2: PDTC114Y; SOT-23
Q3, Q4, Q5: BC846A; SOT-23
R13: 10k; R_0603_1608Metric
R14: 4k7; R_0603_1608Metric
R15, R17, R19: 33k; R_0603_1608Metric
R16, R18, R20: 470R; R_0603_1608Metric
U4: PAM-7Q-0; PAM-7Q0; Manufacturer_Part_Number PAM-7Q-0

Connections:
+3V3: BZ1.1 (-), J5.1, J6.1, J7.2, Q1.2 (D), R13.2, R14.1; also elsewhere on the board
+12V: Q3.2 (C), Q4.2 (C), Q5.2 (C); also elsewhere on the board
/Connectivity/ACC_INT: J6.8; also elsewhere on the board
/Connectivity/Buzzer: Q2.1 (B); also elsewhere on the board
/Connectivity/DRDY: J5.5; also elsewhere on the board
/Connectivity/GPS_EN: Q1.1 (G), R13.1; also elsewhere on the board
/Connectivity/GPS_RX: U4.1 (RXD); also elsewhere on the board
/Connectivity/GPS_TP: U4.6 (TIMEPULSE); also elsewhere on the board
/Connectivity/GPS_TX: U4.2 (TXD); also elsewhere on the board
/Connectivity/GPS_VCC: C24.1, C25.1, Q1.3 (S), U4.4 (VCC), U4.5 (V_BCKP)
/Connectivity/SCL: J5.3, J6.3, J7.3; also elsewhere on the board
/Connectivity/SDA: J5.4, J6.4, J7.4; also elsewhere on the board
/Connectivity/iBuzzer: BZ1.2 (+), Q2.3 (C), R14.2
/Connectivity/iLED_B: D7.3 (BA), R20.1
/Connectivity/iLED_G: D7.2 (GA), R18.1
/Connectivity/iLED_R: D7.1 (RA), R16.1
/Control/LED_B: R19.1; also elsewhere on the board
/Control/LED_G: R17.1; also elsewhere on the board
/Control/LED_R: R15.1; also elsewhere on the board
GND: C24.2, C25.2, D7.4 (K), J5.2, J6.2, J6.7, J7.1, Q2.2 (E), U4.3 (GND), U4.MP1, U4.MP2; also elsewhere on the board
unnamed: Q3.1 (B), R15.2
unnamed: Q3.3 (E), R16.2
unnamed: Q4.1 (B), R17.2
unnamed: Q4.3 (E), R18.2
unnamed: Q5.1 (B), R19.2
unnamed: Q5.3 (E), R20.2

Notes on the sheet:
MCU6050
RGB LED
HMC5883L
GPS peak 71mA
128x64 OLED Display
BUZZER
occhio ai pin nel footprint del led RGB
GPS
Place capacitors close to pins

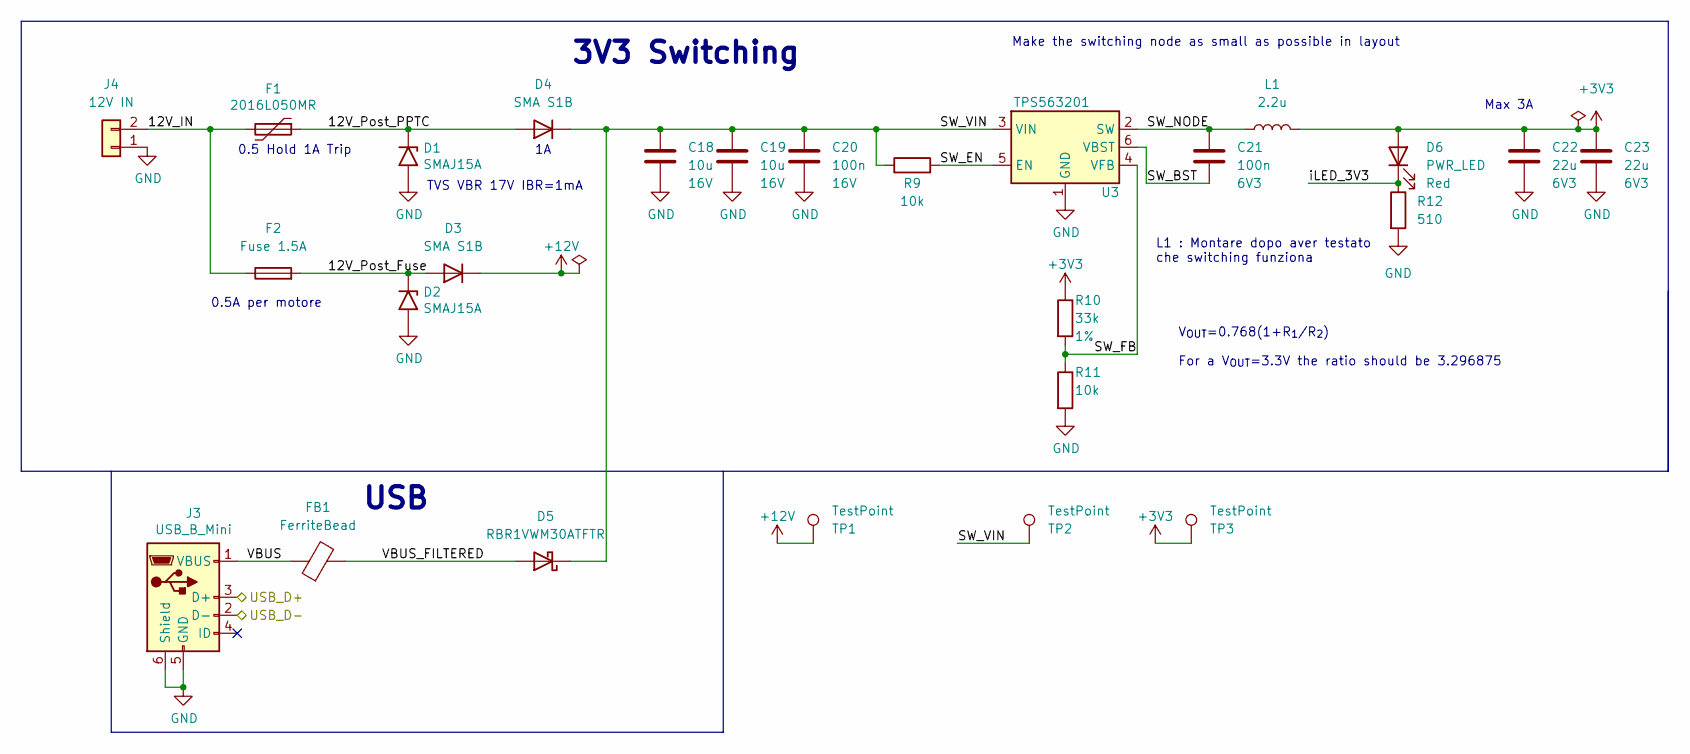
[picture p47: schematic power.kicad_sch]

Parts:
C18, C19: 10u; C_0805_2012Metric; Voltage 16V
C20: 100n; C_0603_1608Metric; Voltage 16V
C21: 100n; C_0603_1608Metric; Voltage 6V3
C22, C23: 22u; C_0805_2012Metric; Voltage 6V3
D1, D2: SMAJ15A; D_SMA
D3, D4: SMA S1B; D_SMA
D5: RBR1VWM30ATFTR; Package-PMDE
D6: PWR_LED; LED_0603_1608Metric
F1: 2016L050MR; 2016L Series PPTC
F2: Fuse 1.5A; Fuse Holder
FB1: FerriteBead; L_0603_1608Metric
J3: USB_B_Mini; USB_Mini-B_Wuerth_65100516121_Horizontal
J4: 12V IN; Molex_Micro-Fit_3.0_43650-0200_1x02_P3.00mm_Horizontal
L1: 2.2u; Inductor
R9, R11: 10k; R_0603_1608Metric
R10: 33k; R_0603_1608Metric; Tolerance 1%
R12: 510; R_0603_1608Metric
TP1, TP2, TP3: TestPoint; TestPoint_Keystone_5005-5009_Compact
U3: TPS563201; SOT-23-6

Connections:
+3V3: C22.1, C23.1, D6.2 (A), L1.2, R10.1, TP3.1; also elsewhere on the board
+12V: D3.1 (K), TP1.1; also elsewhere on the board
/Control/USB_D+: J3.3 (D+); also elsewhere on the board
/Control/USB_D-: J3.2 (D-); also elsewhere on the board
/Power/12V_IN: F1.2, F2.1, J4.2
/Power/12V_Post_Fuse: D2.1 (A1), D3.2 (A), F2.2
/Power/12V_Post_PPTC: D1.1 (A1), D4.2 (A), F1.1
/Power/SW_BST: C21.2, U3.6 (VBST)
/Power/SW_EN: R9.2, U3.5 (EN)
/Power/SW_FB: R10.2, R11.1, U3.4 (VFB)
/Power/SW_NODE: C21.1, L1.1, U3.2 (SW)
/Power/SW_VIN: C18.1, C19.1, C20.1, D4.1 (K), D5.1 (K), R9.1, TP2.1, U3.3 (VIN)
/Power/VBUS: FB1.1, J3.1 (VBUS)
/Power/VBUS_FILTERED: D5.2 (A), FB1.2
/Power/iLED_3V3: D6.1 (K), R12.1
GND: C18.2, C19.2, C20.2, C22.2, C23.2, D1.2 (A2), D2.2 (A2), J3.5 (GND), J3.6 (Shield), J4.1, R11.2, R12.2, U3.1 (GND); also elsewhere on the board

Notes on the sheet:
Max 3A
0.5 Hold 1A Trip
3V3 Switching
0.5A per motore
Make the switching node as small as possible in layout
USB
TVS VBR 17V IBR=1mA
L1 : Montare dopo aver testato che switching funziona
V_{OUT}=0.768(1+R_{1}/R_{2}) For a V_{OUT}=3.3V the ratio should be 3.296875

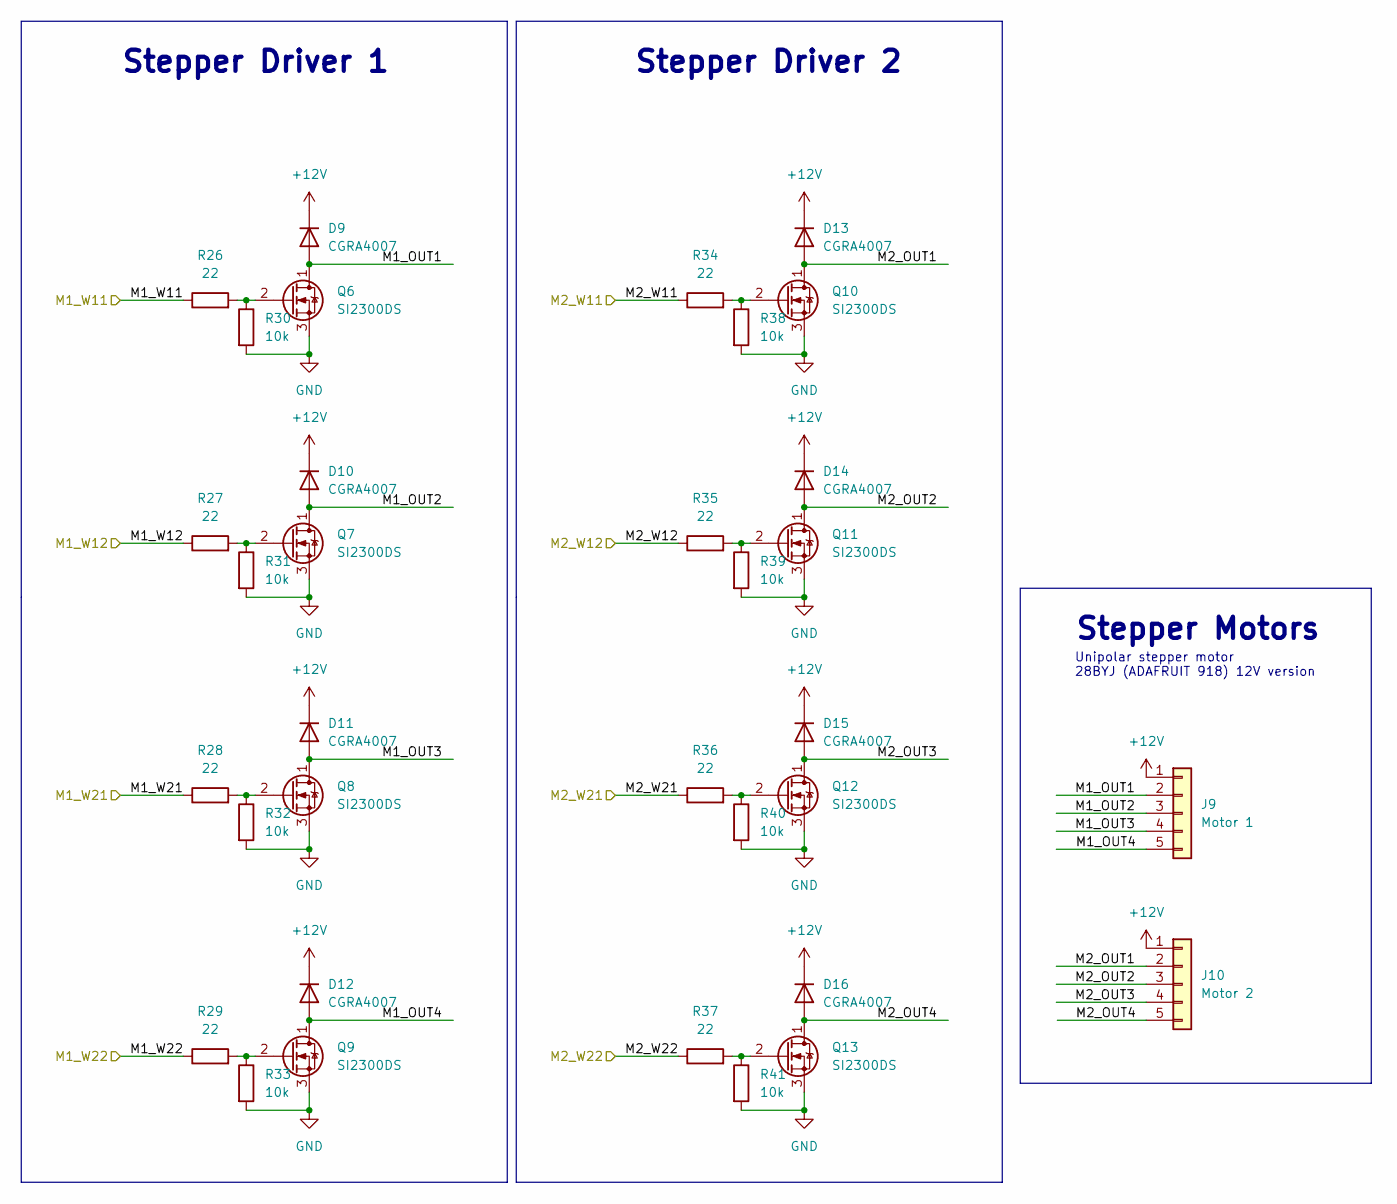
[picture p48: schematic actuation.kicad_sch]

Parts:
D9, D10, D11, D12, D13, D14, D15, D16: CGRA4007; D_SMA
J9: Motor 1; JST_XH_S5B-XH-A_1x05_P2.50mm_Horizontal
J10: Motor 2; JST_XH_S5B-XH-A_1x05_P2.50mm_Horizontal
Q6, Q7, Q8, Q9, Q10, Q11, Q12, Q13: SI2300DS; SOT-23
R26, R27, R28, R29, R34, R35, R36, R37: 22; R_0603_1608Metric
R30, R31, R32, R33, R38, R39, R40, R41: 10k; R_0603_1608Metric

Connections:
+12V: D9.1 (K), D10.1 (K), D11.1 (K), D12.1 (K), D13.1 (K), D14.1 (K), D15.1 (K), D16.1 (K), J9.1, J10.1; also elsewhere on the board
/Actuation/M1_OUT1: D9.2 (A), J9.2, Q6.1 (D)
/Actuation/M1_OUT2: D10.2 (A), J9.3, Q7.1 (D)
/Actuation/M1_OUT3: D11.2 (A), J9.4, Q8.1 (D)
/Actuation/M1_OUT4: D12.2 (A), J9.5, Q9.1 (D)
/Actuation/M1_W11: R26.1; also elsewhere on the board
/Actuation/M1_W12: R27.1; also elsewhere on the board
/Actuation/M1_W21: R28.1; also elsewhere on the board
/Actuation/M1_W22: R29.1; also elsewhere on the board
/Actuation/M2_OUT1: D13.2 (A), J10.2, Q10.1 (D)
/Actuation/M2_OUT2: D14.2 (A), J10.3, Q11.1 (D)
/Actuation/M2_OUT3: D15.2 (A), J10.4, Q12.1 (D)
/Actuation/M2_OUT4: D16.2 (A), J10.5, Q13.1 (D)
/Actuation/M2_W11: R34.1; also elsewhere on the board
/Actuation/M2_W12: R35.1; also elsewhere on the board
/Actuation/M2_W21: R36.1; also elsewhere on the board
/Actuation/M2_W22: R37.1; also elsewhere on the board
GND: Q6.3 (S), Q7.3 (S), Q8.3 (S), Q9.3 (S), Q10.3 (S), Q11.3 (S), Q12.3 (S), Q13.3 (S), R30.2, R31.2, R32.2, R33.2, R38.2, R39.2, R40.2, R41.2; also elsewhere on the board
unnamed: Q6.2 (G), R26.2, R30.1
unnamed: Q7.2 (G), R27.2, R31.1
unnamed: Q8.2 (G), R28.2, R32.1
unnamed: Q9.2 (G), R29.2, R33.1
unnamed: Q10.2 (G), R34.2, R38.1
unnamed: Q11.2 (G), R35.2, R39.1
unnamed: Q12.2 (G), R36.2, R40.1
unnamed: Q13.2 (G), R37.2, R41.1

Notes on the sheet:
Stepper Motors
Unipolar stepper motor 28BYJ (ADAFRUIT 918) 12V version
Stepper Driver 2
Stepper Driver 1

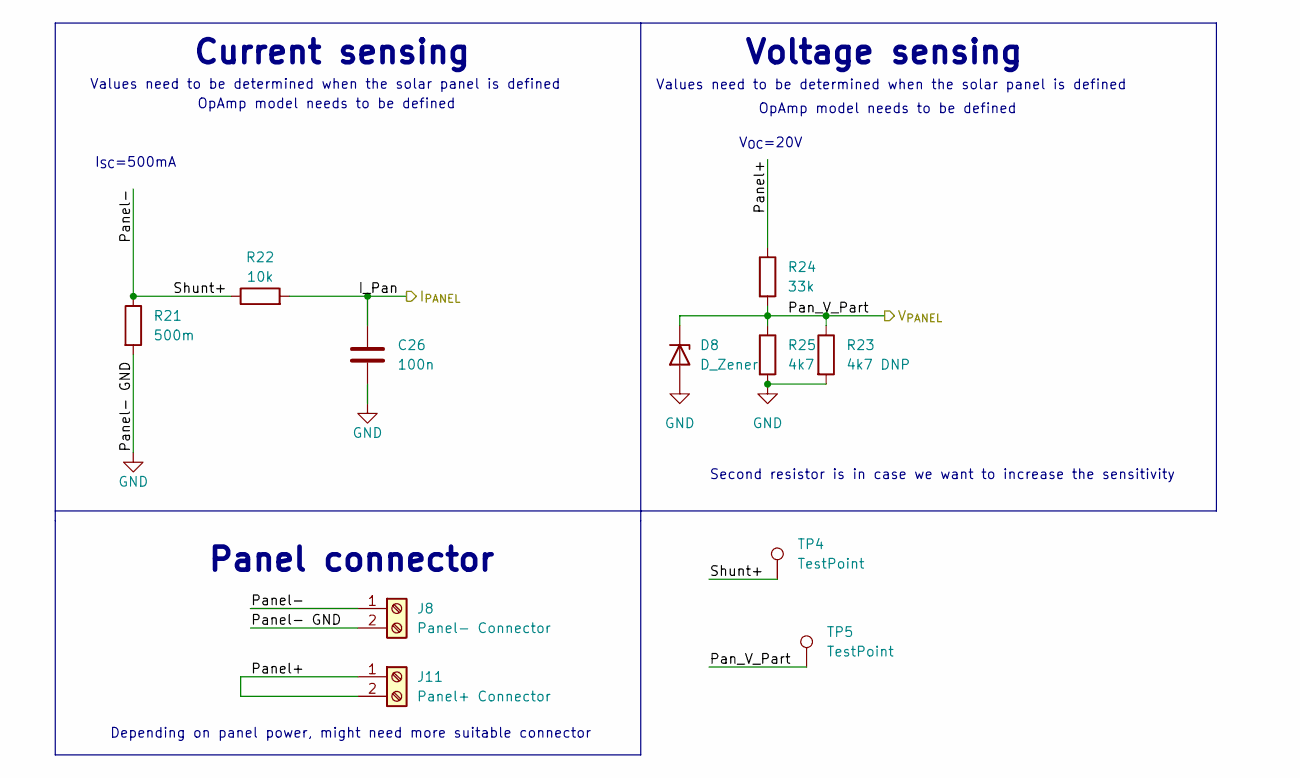
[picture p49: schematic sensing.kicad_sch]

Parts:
C26: 100n; C_0603_1608Metric
D8: D_Zener; D_0603_1608Metric
J8: Panel- Connector; TerminalBlock_TE_282834-2_1x02_P2.54mm_Horizontal
J11: Panel+ Connector; TerminalBlock_TE_282834-2_1x02_P2.54mm_Horizontal
R21: 500m; R_1210_3225Metric
R22: 10k; R_0603_1608Metric
R23: 4k7 DNP; R_0603_1608Metric
R24: 33k; R_0603_1608Metric
R25: 4k7; R_0603_1608Metric
TP4, TP5: TestPoint; TestPoint_Keystone_5005-5009_Compact

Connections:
/Control/I_PANEL: C26.1, R22.2; also elsewhere on the board
/Control/V_PANEL: D8.1 (K), R23.1, R24.2, R25.1, TP5.1; also elsewhere on the board
/Sensing/Panel+: J11.1, J11.2, R24.1
/Sensing/Panel-: J8.1, R21.1, R22.1, TP4.1
GND: C26.2, D8.2 (A), J8.2, R21.2, R23.2, R25.2; also elsewhere on the board

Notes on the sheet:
Values need to be determined when the solar panel is defined
Second resistor is in case we want to increase the sensitivity
Voltage sensing
Current sensing
I_{SC}=500mA
V_{OC}=20V
OpAmp model needs to be defined
Depending on panel power, might need more suitable connector
Panel connector

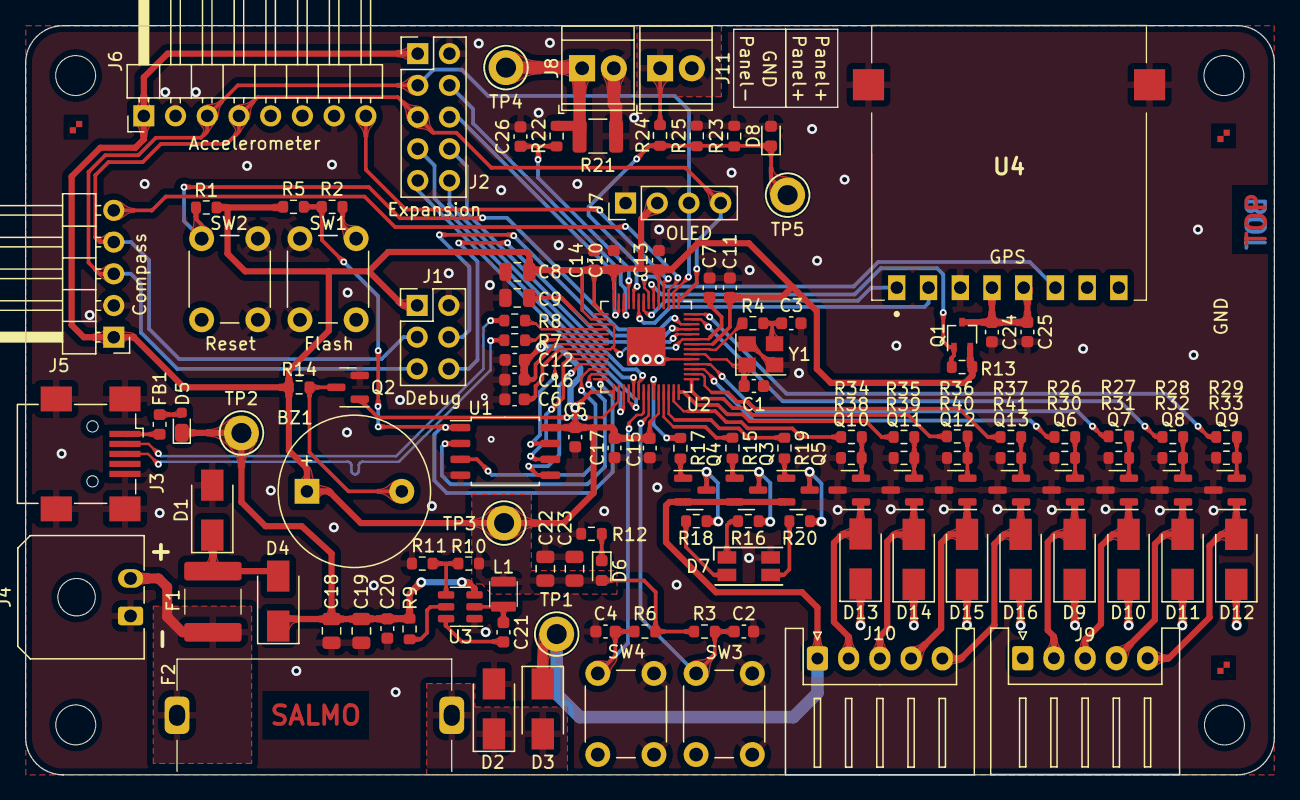
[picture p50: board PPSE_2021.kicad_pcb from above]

Board: 2 copper layers, 100.0 x 60.0 mm, 133 parts (0 on the bottom side), 91 nets.

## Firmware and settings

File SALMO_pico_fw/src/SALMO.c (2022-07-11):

/**
 * @file SALMO.c
 * @author SALMO Society
 * @brief  Finding new way to reach MPPT
 * @version 0.1
 * @date 2022-04-10
 *
 * @copyright Copyright (c) 2022
 *
 */

#include "SALMO.h"
#include <stdio.h>
#include <string.h>
#include <inttypes.h>
#include "pico/stdlib.h"
#include "pico/binary_info.h"
#include "hardware/i2c.h"
#include "hardware/uart.h"
#include "hardware/irq.h"
#include "hardware/pwm.h"
#include "hardware/gpio.h"
#include "../tracking-algorithm/sun_tracker.h"
#include "../MPU6050/MPU6050.h"
#include "../HMC5883L/HMC5883L.h"
#include "../PAM7Q/PAM7Q.h"
#include "../timer/pico_timer.h"
#include "../nmea-parser/minmea.h"
#include "../stepper/pico_stepper.h"
#include "pitches.h"

// Buzzer PWM config
#define SYSCLOCK 125000000

// GPS CONFIG
#define DEBUG_GPS_PARSER
#define GPS_MAX_SENTENCES 12
#define GPS_MAX_SENTENCE_LENGTH 100
char gps_raw_sentences[GPS_MAX_SENTENCES][GPS_MAX_SENTENCE_LENGTH];
int gps_read_lines = 0;

// TIMER CONFIG
bool update_position;
bool read_gps;
bool update_motors_position;
struct repeating_timer update_position_timer;
struct repeating_timer gps_read_timer;
struct repeating_timer update_motors_position_timer;
#define UPDATE_SUN_POSITION_TIMER_PERIOD_MS 4000
#define GPS_READ_TIMER_PERIOD_MS 4000
#define UPDATE_MOTORS_POSITION_TIMER_PERIOD_MS 9900 // 100ms are for sleep between buzzer on and off

// SALMO Functions state
bool tracking_enable_pressed = false;
bool go_home_enable_pressed = false;

// GLOBAL VARS
Place gps_parsed_place;
PicoStepper stepper1 = {0};
PicoStepper stepper2 = {0};
struct minmea_sentence_rmc frame_rmc;
struct minmea_sentence_gga frame_gga;

float compute_compass_degree();
float compute_acc_degree();
int calculate_steps(float current_angle, float desired_angle);
void go_home(PicoStepper *stepper1, PicoStepper *stepper2);
void move_motors_to_the_sun(Position *pos, PicoStepper *stepper1, PicoStepper *stepper2);
void nmea_parse(const char *msg, Place *parsed_place);
void init_position_timer(int time_ms);
void init_motors_timer(int time_ms);
void init_gps_timer(int time_ms);
void gpio_irq_callback(uint gpio, uint32_t events);
void beep_on(uint16_t freq, uint8_t duty_perc);
void beep_off();
void tone(uint8_t freq, unsigned long duration_ms);
void startup_tone();

void hello_salmo()
{
    printf(
        "\r\n"
        "███████  █████  ██      ███    ███  ██████  \r\n"
        "██      ██   ██ ██      ████  ████ ██    ██ \r\n"
        "███████ ███████ ██      ██ ████ ██ ██    ██ \r\n"
        "     ██ ██   ██ ██      ██  ██  ██ ██    ██ \r\n"
        "███████ ██   ██ ███████ ██      ██  ██████  \r\n\r\n");
}

/**
 * @brief GPS read timer callback
 *
 * @param t gps timer
 */
bool gps_read_callback(struct repeating_timer *t)
{
    read_gps = true;
    return read_gps;
}

/**
 * @brief Set update position flag every t.delay_us
 * @param t Pointer to the timer structure
 */
bool update_position_callback(struct repeating_timer *t)
{
    // printf("Update motor position tim elapsed -> Time: %lld\n", time_us_64());
    update_position = true;
    return update_position;
}

/**
 * @brief Set update position flag every t.delay_us
 * @param t Pointer to the timer structure
 */
bool update_motors_position_callback(struct repeating_timer *t)
{
    // printf("Update motor position tim elapsed -> Time: %lld\n", time_us_64());
    update_motors_position = true;
    return update_motors_position;
}

int main()
{

    /* Used variables */
    int16_t acc_gyro_data = 0;
    Position sun_position;
    char gps_rx_buffer[100];

#ifdef GPS_SIMULATIOR
    // Sample place and its respective conversion into sun position
    Place manual_place = {2030, 2, 28, 10, 10, 10, 55.751244, 37.618423};
    Position manual_position = compute_complete_position(&manual_place);
#endif

// #define FAMOUS_CITIES_SIMULATION
#ifdef FAMOUS_CITIES_SIMULATION
    Place rome = {2022, 6, 5, 10, 0, 20, 41.9027835, 12.4963655};
    Position rome_position = compute_complete_position(&rome);

    // TODO: check why minutes are not mapped correctly
    Place berlin = {2022, 6, 5, 12, 40, 00, 52.520008, 13.404954};
    Position berlin_position = compute_complete_position(&berlin);

    Place rio = {2022, 6, 5, 18, 00, 00, -22.908333, -43.196388};
    Position rio_position = compute_complete_position(&rio);
#endif

    /* Initialization of peripherals*/

    // stdio_init_all();  // equals to usb and uart init
    stdio_usb_init();  // initialize usb cdc
    stdio_uart_init(); // initialize uart0 with 0 baud rate
    PAM7Q_init(UART1_TX, UART1_RX);

#ifdef INTERRUPTS_ARE_WORKING
    irq_set_exclusive_handler(UART1_IRQ, on_uart_rx);
    irq_set_enabled(UART1_IRQ, true);
    uart_set_irq_enables(GPS_UART_ID, false, false);
#endif

    /* SET GPS ENABLE PIN */
    gpio_init(GPS_EN);
    gpio_set_dir(GPS_EN, GPIO_OUT);
    gpio_put(GPS_EN, 0); // with zero it's enabled

    update_position = false;

    /* Stepper motors initialization  */
    picoStepperInit(&stepper1, M1_W11, M1_W12, M1_W21, M1_W22, STEPS_PER_REV, INITIAL_SPEED); // stepper1 = yaw
    picoStepperInit(&stepper2, M2_W11, M2_W12, M2_W21, M2_W22, STEPS_PER_REV, INITIAL_SPEED); // stepper2 = pitch

    /* SET HOME AND GPS_ENABLE SWITCH  */
    gpio_init(NOT_HOME_SW);
    gpio_init(NOT_EN_SW);
    gpio_set_dir(NOT_HOME_SW, GPIO_IN);
    gpio_set_dir(NOT_EN_SW, GPIO_IN);
    gpio_set_input_enabled(NOT_HOME_SW, true);
    gpio_set_input_enabled(NOT_EN_SW, true);
    gpio_pull_up(NOT_HOME_SW);
    gpio_pull_up(NOT_EN_SW);
    // gpio irq handler - NOTE: Currently the GPIO parameter is ignored, and this callback will be called for any enabled GPIO IRQ on any pin.
    gpio_set_irq_enabled_with_callback(NOT_HOME_SW, GPIO_IRQ_EDGE_RISE, true, &gpio_irq_callback);
    gpio_set_irq_enabled_with_callback(NOT_EN_SW, GPIO_IRQ_EDGE_RISE, true, &gpio_irq_callback);

    /* SET I2C Pins */
    gpio_set_function(I2C1_SDA, GPIO_FUNC_I2C);
    gpio_set_function(I2C1_SCL, GPIO_FUNC_I2C);
    // Make the I2C pins available to picotool
    bi_decl(bi_2pins_with_func(I2C1_SDA, I2C1_SCL, GPIO_FUNC_I2C));
    i2c_init(I2C_PERIPHERAL, I2C_PORT1_BAUD_RATE);

    /* Verify if are needed, probably they are already in the sensor breakout board
        gpio_pull_up(I2C1_SDA);
        gpio_pull_up(I2C1_SCL);
    */

    // Init i2c port1 with defined baud rate
    // I2C MPU port is defined inside every .h device library

    /* Startup message with relative delay */
    sleep_ms(2000);
    hello_salmo();
    startup_tone();
    printf("Peripherals initialization...\r\n");

    /* MPU6050 Initialization */
    MPU6050_Initialize();
    if (MPU6050_TestConnection())
    {
        printf("MPU6050 connection success\n");
    }
    else
    {
        printf("MPU6050 connection failed\n");
    }
    MPU6050_GetRawAccelGyro(&acc_gyro_data);

    HMC5883L_initialize();
    if (isHMC())
    {
        printf("HMC5883L connection success\n");
    }
    else
    {
        printf("HMC5883L connection failed\n");
    }
    compute_compass_degree();

    /* Timers initialization */
    init_position_timer(UPDATE_SUN_POSITION_TIMER_PERIOD_MS);
    init_gps_timer(GPS_READ_TIMER_PERIOD_MS);
    init_motors_timer(UPDATE_MOTORS_POSITION_TIMER_PERIOD_MS);

    while (true)
    {
        /* Go home button relative behaviour */
        if (go_home_enable_pressed)
        {
            beep_on(2000, 50);
            sleep_ms(100);
            beep_off();
            go_home(&stepper1, &stepper2);
            go_home_enable_pressed = false;
            tracking_enable_pressed = false;
        }
        /* Tracking button relative behaviour */
        if (tracking_enable_pressed)
        {   
            beep_on(2000, 50);
            sleep_ms(100);
            beep_off();
            if (frame_gga.satellites_tracked < 1)
            {
                printf("ERROR: Zero satellites available to track the sun, please wait...\r\n");
                tracking_enable_pressed = false;
            }
            /* When relative timer elapses the motors are powered */
            if (update_motors_position && frame_gga.satellites_tracked > 0)
            {
                move_motors_to_the_sun(&sun_position, &stepper1, &stepper2);
                update_motors_position = false;
            }
        }
        if (read_gps)
        {
            gps_read_lines = 0;
            memset(gps_rx_buffer, 0, sizeof(gps_rx_buffer));
            while (gps_read_lines < GPS_MAX_SENTENCES)
            {
                while (uart_is_readable(GPS_UART_ID))
                {
                    char ch = uart_getc(GPS_UART_ID);
                    strncat(gps_rx_buffer, &ch, 1);
                    if (ch == '\n')
                    {
                        strncat(gps_rx_buffer, '\0', 1);
                        strcpy(gps_raw_sentences[gps_read_lines], gps_rx_buffer);
                        memset(gps_rx_buffer, 0, sizeof(gps_rx_buffer));
                        gps_read_lines++;
                    }
                }
            }
            printf("--------->GPS PARSING\r\n\r\n");
            read_gps = false;
            for (int i = 0; i < GPS_MAX_SENTENCES; i++)
            {
#ifdef DEBUG_GPS_PARSER
                printf("\tPARSED LINE%d | %s\r\n", i, gps_raw_sentences[i]);
#endif
                nmea_parse(gps_raw_sentences[i], &gps_parsed_place);
            }
            print_place(&gps_parsed_place);
            printf("\tTotal number of satellites available: %d \r\n\r\n", frame_gga.satellites_tracked);
            printf("<---------END OF GPS PARSING\r\n");
        }

        if (update_position)
        {
#ifdef FAMOUS_CITIES_SIMULATION
            /* Simulate sun position of some famous cities with fixed position and hour*/
            printf("[ROME] ");
            print_place(&rome);
            printf("[ROME] Position elevation %f azimuth %f \r\n\r\n", rome_position.elevation, rome_position.azimuth);

            printf("[BERLIN] ");
            print_place(&berlin);
            printf("[BERLIN] Position elevation %f azimuth %f \r\n\r\n", berlin_position.elevation, berlin_position.azimuth);

            printf("[RIO] ");
            print_place(&rio);
            printf("[RIO] Position elevation %f azimuth %f \r\n\r\n", rio_position.elevation, rio_position.azimuth);
#endif

#ifdef GPS_SIMULATOR
            /* Simulate sun position based on a manual position hardcoded which canges over time*/
            print_place(&manual_place);
            manual_position = compute_complete_position(&manual_place);
            printf("[MANUAL] Position elevation %f azimuth %f \r\n\r\n", manual_position.elevation, manual_position.azimuth);
            if (manual_place.hour + 1 > 23)
            {
                manual_place.hour = 0;
                manual_place.day++;
            }
            else
            {
                manual_place.hour++;
            };
#endif

            /* Compute sun position */
            sun_position = compute_complete_position(&gps_parsed_place);
            printf("--------->SUN POSITION AND MCU STATUS\r\n\r\n");
            if (frame_gga.satellites_tracked > 0)
            {
                printf("\tSun elevation %f azimuth %f \r\n\r\n", sun_position.elevation, sun_position.azimuth);

                printf("\tGo home active?: %s, Tracking active?: %s \r\n\r\n", go_home_enable_pressed ? "true" : "false", tracking_enable_pressed ? "true" : "false");
                printf("<---------END OF SUN POSITION AND MCU STATUS\r\n");
            }
            else
            {
                printf("\t GPS SIGNAL Weak! \r\n\tWaiting for more satellites...\r\n");
            }
            update_position = false;
        }
    }

    return 0;
}

/**
 * @brief gpio irq callback
 *
 * @param gpio gpio number
 * @param events irq event
 */
void gpio_irq_callback(uint gpio, uint32_t events)
{
    // printf("GPIO TRIGGERED\r\n");
    if (gpio == NOT_HOME_SW)
    {
        printf("Home button pressed\n");
        go_home_enable_pressed = !go_home_enable_pressed;
    }
    else if (gpio == NOT_EN_SW)
    {
        printf("Tracking enable pressed \r\n");
        tracking_enable_pressed = !tracking_enable_pressed;
    }
}

/**
 * @brief Initialize the timer for position update
 *
 * @param time_ms Timer delay in milliseconds
 */
void init_position_timer(int time_ms)
{
    add_repeating_timer_ms(time_ms, update_position_callback, NULL, &update_position_timer);
}

/**
 * @brief Initialize the timer for gps update
 *
 * @param time_ms Timer delay in milliseconds
 */
void init_motors_timer(int time_ms)
{
    add_repeating_timer_ms(time_ms, update_motors_position_callback, NULL, &update_motors_position_timer);
}

/**
 * @brief Initialize the timer for gps update
 *
 * @param time_ms Timer delay in milliseconds
 */
void init_gps_timer(int time_ms)
{
    add_repeating_timer_ms(time_ms, gps_read_callback, NULL, &gps_read_timer);
}

/**
 * @brief compute compass headings in degree
 * @return compass heading in degree
 */
float compute_compass_degree()
{
    int16_t HMCx = 0;
    int16_t HMCy = 0;
    int16_t HMCz = 0;
    HMC5883L_getHeading(&HMCx, &HMCy, &HMCz);

    // Assuming Z axis is pointing up, Y axis is pointing straight out of the panel and X axis is pointing to the right
    float compass_radians = atan2(HMCx, HMCy); // note: atan2(y,x) = tan^-1 (arg1/arg2) and auto matches the quadrant
    return compass_radians * 180 / M_PI;
}

/**
 * @brief compute accelerometer headings in degree
 * @return accelerometer heading in degree
 */
float compute_acc_degree()
{
    int16_t AccGyro[6];
    int16_t AccX = 0;
    int16_t AccY = 0;
    int16_t AccZ = 0;

    MPU6050_GetRawAccelGyro(AccGyro);
    AccX = AccGyro[0];
    AccY = AccGyro[1];
    AccZ = AccGyro[2];

    // assuming Z axis is pointing up when the panel is flat
    float tilt_radians = atan2(sqrt(pow(AccX, 2) + pow(AccY, 2)), AccZ);
    return tilt_radians * 180 / M_PI;
}

/**
 * @brief calculate steps to move given the current heading and the desired heading
 * @param current_heading current heading in degree
 * @param desired_heading desired heading in degree
 * @return steps to move
 */
int calculate_steps(float current_angle, float desired_angle)
{
    float angle_per_step = 360 / STEPS_PER_REV;
    float steps_to_move = (desired_angle - current_angle) / angle_per_step;
    return round(steps_to_move);
}

/**
 * @brief Move motors to home position
 *
 */
void go_home(PicoStepper *stepper1, PicoStepper *stepper2)
{
    printf("Compass: %.3f', Gyro: %.3f', rotating towards NORD at 45' tilt\n", compute_compass_degree(), compute_acc_degree());
    // yaw (stepper1) for X steps to get to compass headings=0°
    setSpeed(stepper1, 100);
    printf("MOTOR 1 STEPS: %d, MOTOR 2 STEPS %d \r\n", calculate_steps(compute_compass_degree(), 0), calculate_steps(compute_acc_degree(), 45));
    step(stepper1, calculate_steps(compute_compass_degree(), 0));
    // ypitch (stepper2) for X steps to get to acc headings=45°
    setSpeed(stepper2, 100);
    step(stepper2, calculate_steps(compute_acc_degree(), 45));
}

/**
 * @brief Move motors until they will be alligned to the sun position
 *
 */
void move_motors_to_the_sun(Position *pos, PicoStepper *stepper1, PicoStepper *stepper2)
{
    // Sun elevation must meet accelerometer
    int elevation_step = calculate_steps(compute_acc_degree(), pos->elevation);
    // Sun azimuth must meet compass
    int azimuth_step = calculate_steps(compute_compass_degree(), pos->azimuth);

    printf("Tracking on! \r\nElevation step to do: %d, Azimuth step to do: %d\r\n", elevation_step, azimuth_step);
    setSpeed(stepper1, 100);
    setSpeed(stepper2, 100);
    step(stepper1, azimuth_step);
    step(stepper2, elevation_step);
}

/**
 * @brief Parse nmea sentence and store the information into parsed_place
 * Actually this function is working just with RMC and GGA sentences,
 * which are the minimal sentences required to build a Place structure
 *
 * @param msg NMEA Sentence
 * @param parsed_place Place structure to store the information
 */
void nmea_parse(const char *msg, Place *parsed_place)
{
    uint8_t nmea_id = minmea_sentence_id(msg, false);

    switch (nmea_id)
    {

    case MINMEA_SENTENCE_RMC:
        minmea_parse_rmc(&frame_rmc, msg);
#ifdef NMEA_DEBUG
        printf("[20%d:%d:%d][20YY:MM:DD] \r\n", frame_rmc.date.year, frame_rmc.date.month, frame_rmc.date.day);
#endif
        parsed_place->year = 2000 + frame_rmc.date.year;
        parsed_place->month = frame_rmc.date.month;
        parsed_place->day = frame_rmc.date.day;
        break;

    case MINMEA_SENTENCE_GGA:
        minmea_parse_gga(&frame_gga, msg);
#ifdef NMEA_DEBUG
        printf("[%d:%d:%d][HH:MM:SS]\r\n", frame_gga.time.hours, frame_gga.time.minutes, frame_gga.time.seconds);
        printf("Computed latitude: %.2f, Computed longitude: %.2f \r\n", minmea_tocoord(&frame_gga.latitude), minmea_tocoord(&frame_gga.longitude));
#endif
        parsed_place->hour = frame_gga.time.hours;
        parsed_place->minute = frame_gga.time.minutes;
        parsed_place->second = (double)frame_gga.time.seconds;
        parsed_place->latitude = minmea_tocoord(&frame_gga.latitude);
        parsed_place->longitude = minmea_tocoord(&frame_gga.longitude);
        break;

    default:
        break;
    }
}

void beep_on(uint16_t freq, uint8_t duty_perc)
{
    // Buzzer PWM settings
    // ES: We want a frequency of 2KHz (500us period) and a duty cycle of 50%
    // System clock is running at 125Mhz (8ns period)
    // In order to output a 2KHz square wave we should count from 0 to 500us/8ns=62500
    // When counter reach 62500 we change the state of the pin
    gpio_set_function(BUZZ_EN, GPIO_FUNC_PWM);
    pwm_set_wrap(0, SYSCLOCK / freq);
    pwm_set_chan_level(0, PWM_CHAN_A, (SYSCLOCK / freq) * duty_perc);
    pwm_set_enabled(0, true);
}

void beep_off()
{
    pwm_set_enabled(0, false);
}

void tone(uint8_t freq, unsigned long duration_ms)
{
    beep_on(freq, 50);
    sleep_ms(duration_ms);
    beep_off();
}

void startup_tone()
{
    int noteDuration = 0;
    int pauseBetweenNotes = 0;

    int melody[] = {
        NOTE_A5, NOTE_A5, NOTE_A5, NOTE_E5, NOTE_D5, NOTE_FS5,
        NOTE_FS5, NOTE_FS5, NOTE_E5, NOTE_E5, NOTE_FS5, NOTE_E5};

    // note durations: 4 = quarter note, 8 = eighth note, etc.:
    int noteDurations[] = {
        8, 8, 8, 4, 4, 4,
        4, 5, 8, 8, 8, 8};

    for (int i = 0; i < sizeof(melody) / sizeof(int); i++)
    {
        // to calculate the note duration, take one second divided by the note type.
        // e.g. quarter note = 1000 / 4, eighth note = 1000/8, etc.
        noteDuration = 1000 / noteDurations[i];
        tone(melody[i], noteDuration);
        // to distinguish the notes, set a minimum time between them.
        // the note's duration + 30% seems to work well:
        pauseBetweenNotes = noteDuration * 0.2;
        sleep_ms(pauseBetweenNotes);
    }
}

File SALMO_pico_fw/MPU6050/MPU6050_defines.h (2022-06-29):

#ifndef _MPU6050_DEFINES_H_
#define _MPU6050_DEFINES_H_

#define MPU6050_ADDRESS_AD0_LOW     0x68 // address pin low (GND), default for InvenSense evaluation board
#define MPU6050_ADDRESS_AD0_HIGH    0x69 // address pin high (VCC)
#define MPU6050_DEFAULT_ADDRESS     (MPU6050_ADDRESS_AD0_LOW<<1)

#define MPU6050_RA_XG_OFFS_TC       0x00 //[7] PWR_MODE, [6:1] XG_OFFS_TC, [0] OTP_BNK_VLD
#define MPU6050_RA_YG_OFFS_TC       0x01 //[7] PWR_MODE, [6:1] YG_OFFS_TC, [0] OTP_BNK_VLD
#define MPU6050_RA_ZG_OFFS_TC       0x02 //[7] PWR_MODE, [6:1] ZG_OFFS_TC, [0] OTP_BNK_VLD
#define MPU6050_RA_X_FINE_GAIN      0x03 //[7:0] X_FINE_GAIN
#define MPU6050_RA_Y_FINE_GAIN      0x04 //[7:0] Y_FINE_GAIN
#define MPU6050_RA_Z_FINE_GAIN      0x05 //[7:0] Z_FINE_GAIN
#define MPU6050_RA_XA_OFFS_H        0x06 //[15:0] XA_OFFS
#define MPU6050_RA_XA_OFFS_L_TC     0x07
#define MPU6050_RA_YA_OFFS_H        0x08 //[15:0] YA_OFFS
#define MPU6050_RA_YA_OFFS_L_TC     0x09
#define MPU6050_RA_ZA_OFFS_H        0x0A //[15:0] ZA_OFFS
#define MPU6050_RA_ZA_OFFS_L_TC     0x0B
#define MPU6050_RA_XG_OFFS_USRH     0x13 //[15:0] XG_OFFS_USR
#define MPU6050_RA_XG_OFFS_USRL     0x14
#define MPU6050_RA_YG_OFFS_USRH     0x15 //[15:0] YG_OFFS_USR
#define MPU6050_RA_YG_OFFS_USRL     0x16
#define MPU6050_RA_ZG_OFFS_USRH     0x17 //[15:0] ZG_OFFS_USR
#define MPU6050_RA_ZG_OFFS_USRL     0x18
#define MPU6050_RA_SMPLRT_DIV       0x19
#define MPU6050_RA_CONFIG           0x1A
#define MPU6050_RA_GYRO_CONFIG      0x1B
#define MPU6050_RA_ACCEL_CONFIG     0x1C
#define MPU6050_RA_FF_THR           0x1D
#define MPU6050_RA_FF_DUR           0x1E
#define MPU6050_RA_MOT_THR          0x1F
#define MPU6050_RA_MOT_DUR          0x20
#define MPU6050_RA_ZRMOT_THR        0x21
#define MPU6050_RA_ZRMOT_DUR        0x22
#define MPU6050_RA_FIFO_EN          0x23
#define MPU6050_RA_I2C_MST_CTRL     0x24
#define MPU6050_RA_I2C_SLV0_ADDR    0x25
#define MPU6050_RA_I2C_SLV0_REG     0x26
#define MPU6050_RA_I2C_SLV0_CTRL    0x27
#define MPU6050_RA_I2C_SLV1_ADDR    0x28
#define MPU6050_RA_I2C_SLV1_REG     0x29
#define MPU6050_RA_I2C_SLV1_CTRL    0x2A
#define MPU6050_RA_I2C_SLV2_ADDR    0x2B
#define MPU6050_RA_I2C_SLV2_REG     0x2C
#define MPU6050_RA_I2C_SLV2_CTRL    0x2D
#define MPU6050_RA_I2C_SLV3_ADDR    0x2E
#define MPU6050_RA_I2C_SLV3_REG     0x2F
#define MPU6050_RA_I2C_SLV3_CTRL    0x30
#define MPU6050_RA_I2C_SLV4_ADDR    0x31
#define MPU6050_RA_I2C_SLV4_REG     0x32
#define MPU6050_RA_I2C_SLV4_DO      0x33
#define MPU6050_RA_I2C_SLV4_CTRL    0x34
#define MPU6050_RA_I2C_SLV4_DI      0x35
#define MPU6050_RA_I2C_MST_STATUS   0x36
#define MPU6050_RA_INT_PIN_CFG      0x37
#define MPU6050_RA_INT_ENABLE       0x38
#define MPU6050_RA_DMP_INT_STATUS   0x39
#define MPU6050_RA_INT_STATUS       0x3A
#define MPU6050_RA_ACCEL_XOUT_H     0x3B
#define MPU6050_RA_ACCEL_XOUT_L     0x3C
#define MPU6050_RA_ACCEL_YOUT_H     0x3D
#define MPU6050_RA_ACCEL_YOUT_L     0x3E
#define MPU6050_RA_ACCEL_ZOUT_H     0x3F
#define MPU6050_RA_ACCEL_ZOUT_L     0x40
#define MPU6050_RA_TEMP_OUT_H       0x41
#define MPU6050_RA_TEMP_OUT_L       0x42
#define MPU6050_RA_GYRO_XOUT_H      0x43
#define MPU6050_RA_GYRO_XOUT_L      0x44
#define MPU6050_RA_GYRO_YOUT_H      0x45
#define MPU6050_RA_GYRO_YOUT_L      0x46
#define MPU6050_RA_GYRO_ZOUT_H      0x47
#define MPU6050_RA_GYRO_ZOUT_L      0x48
#define MPU6050_RA_EXT_SENS_DATA_00 0x49
#define MPU6050_RA_EXT_SENS_DATA_01 0x4A
#define MPU6050_RA_EXT_SENS_DATA_02 0x4B
#define MPU6050_RA_EXT_SENS_DATA_03 0x4C
#define MPU6050_RA_EXT_SENS_DATA_04 0x4D
#define MPU6050_RA_EXT_SENS_DATA_05 0x4E
#define MPU6050_RA_EXT_SENS_DATA_06 0x4F
#define MPU6050_RA_EXT_SENS_DATA_07 0x50
#define MPU6050_RA_EXT_SENS_DATA_08 0x51
#define MPU6050_RA_EXT_SENS_DATA_09 0x52
#define MPU6050_RA_EXT_SENS_DATA_10 0x53
#define MPU6050_RA_EXT_SENS_DATA_11 0x54
#define MPU6050_RA_EXT_SENS_DATA_12 0x55
#define MPU6050_RA_EXT_SENS_DATA_13 0x56
#define MPU6050_RA_EXT_SENS_DATA_14 0x57
#define MPU6050_RA_EXT_SENS_DATA_15 0x58
#define MPU6050_RA_EXT_SENS_DATA_16 0x59
#define MPU6050_RA_EXT_SENS_DATA_17 0x5A
#define MPU6050_RA_EXT_SENS_DATA_18 0x5B
#define MPU6050_RA_EXT_SENS_DATA_19 0x5C
#define MPU6050_RA_EXT_SENS_DATA_20 0x5D
#define MPU6050_RA_EXT_SENS_DATA_21 0x5E
#define MPU6050_RA_EXT_SENS_DATA_22 0x5F
#define MPU6050_RA_EXT_SENS_DATA_23 0x60
#define MPU6050_RA_MOT_DETECT_STATUS    0x61
#define MPU6050_RA_I2C_SLV0_DO      0x63
#define MPU6050_RA_I2C_SLV1_DO      0x64
#define MPU6050_RA_I2C_SLV2_DO      0x65
#define MPU6050_RA_I2C_SLV3_DO      0x66
#define MPU6050_RA_I2C_MST_DELAY_CTRL   0x67
#define MPU6050_RA_SIGNAL_PATH_RESET    0x68
#define MPU6050_RA_MOT_DETECT_CTRL      0x69
#define MPU6050_RA_USER_CTRL        0x6A
#define MPU6050_RA_PWR_MGMT_1       0x6B
#define MPU6050_RA_PWR_MGMT_2       0x6C
#define MPU6050_RA_BANK_SEL         0x6D
#define MPU6050_RA_MEM_START_ADDR   0x6E
#define MPU6050_RA_MEM_R_W          0x6F
#define MPU6050_RA_DMP_CFG_1        0x70
#define MPU6050_RA_DMP_CFG_2        0x71
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

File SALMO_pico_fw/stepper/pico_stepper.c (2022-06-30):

/*
 * pico_stepper.c - Stepper library for Raspberry Pi Pico - Version 0.1
 *
 * Copyright (C) Beshr Kayali
 * Copyright (C) Lisa Santarossa, Tommaso Canova, Thomas Nonis, Gabriele Berretta, Simone Tollardo
 *
 * Based on Arduino Stepper Library
 * Copyright (C) Arduino LLC. Copyright (C) Sebastian Gassner. Copyright (c) Noah Shibley.
 *
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
 */

// #include <cstdlib>
#include "pico/stdlib.h"
#include "pico/time.h"
#include "pico_stepper.h"

void picoStepperInit(PicoStepper *stepper, int pin1, int pin2, int pin3, int pin4, int total_steps, long initial_speed)
{
  stepper->total_steps = total_steps;
  stepper->initial_speed = initial_speed;
  stepper->dir = 0;
  stepper->delay = 60L * 1000L * 1000L / stepper->total_steps / stepper->initial_speed;
  stepper->current_step = 0;
  stepper->last_step_us_time = 0;
  stepper->pin1 = pin1;
  stepper->pin2 = pin2;
  stepper->pin3 = pin3;
  stepper->pin4 = pin4;
  gpio_init(stepper->pin1);
  gpio_init(stepper->pin2);
  gpio_init(stepper->pin3);
  gpio_init(stepper->pin4);
  gpio_set_dir(stepper->pin1, GPIO_OUT);
  gpio_set_dir(stepper->pin2, GPIO_OUT);
  gpio_set_dir(stepper->pin3, GPIO_OUT);
  gpio_set_dir(stepper->pin4, GPIO_OUT);
  // Turn off pins to reduce power consumption
  gpio_put(stepper->pin1, 0);
  gpio_put(stepper->pin2, 0);
  gpio_put(stepper->pin3, 0);
  gpio_put(stepper->pin4, 0);
}

void setSpeed(PicoStepper *stepper, long speed)
{
  stepper->delay = 60L * 1000L * 1000L / stepper->total_steps / speed;
}

void step(PicoStepper *stepper, int steps_to_move)
{
  int steps_left = steps_to_move >= 0 ? steps_to_move : steps_to_move * -1; // abs value check
  // abs(steps_to_move);

  if (steps_to_move > 0)
  {
    stepper->dir = 1;
  }
  else
  {
    stepper->dir = 0;
  }

  while (steps_left > 0)
  {
    uint64_t now = to_us_since_boot(get_absolute_time());

    if (now - stepper->last_step_us_time >= stepper->delay)
    {
      stepper->last_step_us_time = now;

      if (stepper->dir == 1)
      {
        stepper->current_step++;

        if (stepper->current_step == stepper->total_steps)
        {
          stepper->current_step = 0;
        }
      }
      else
      {
        if (stepper->current_step == 0)
        {
          stepper->current_step = stepper->total_steps;
        }

        stepper->current_step--;
      }

      stepMotor(stepper, stepper->current_step % 4);
      steps_left--;
    }
  }

  // Turn off pins to reduce power consumption
  gpio_put(stepper->pin1, 0);
  gpio_put(stepper->pin2, 0);
  gpio_put(stepper->pin3, 0);
  gpio_put(stepper->pin4, 0);
}

void stepMotor(PicoStepper *stepper, int step)
{
  switch (step)
  {
  case 0: // 1000
    gpio_put(stepper->pin1, 1);
    gpio_put(stepper->pin2, 0);
    gpio_put(stepper->pin3, 0);
    gpio_put(stepper->pin4, 0);
    break;

  case 1: // 0100
    gpio_put(stepper->pin1, 0);
    gpio_put(stepper->pin2, 1);
    gpio_put(stepper->pin3, 0);
    gpio_put(stepper->pin4, 0);
    break;

  case 2: // 0010
    gpio_put(stepper->pin1, 0);
    gpio_put(stepper->pin2, 0);
    gpio_put(stepper->pin3, 1);
    gpio_put(stepper->pin4, 0);
    break;

  case 3: // 0001
    gpio_put(stepper->pin1, 0);
    gpio_put(stepper->pin2, 0);
    gpio_put(stepper->pin3, 0);
    gpio_put(stepper->pin4, 1);
    break;
  }
}

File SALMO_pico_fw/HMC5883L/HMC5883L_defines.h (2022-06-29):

#ifndef _MPU6050_DEFINES_H_
#define _MPU6050_DEFINES_H_

//Device address
#define HMC5883L_DEFAULT_ADDRESS    0x1E

//Register map
#define HMC5883L_RA_CONFIG_A        0x00
#define HMC5883L_RA_CONFIG_B        0x01
#define HMC5883L_RA_MODE            0x02
#define HMC5883L_RA_DATAX_H         0x03
#define HMC5883L_RA_DATAX_L         0x04
#define HMC5883L_RA_DATAZ_H         0x05
#define HMC5883L_RA_DATAZ_L         0x06
#define HMC5883L_RA_DATAY_H         0x07
#define HMC5883L_RA_DATAY_L         0x08
#define HMC5883L_RA_STATUS          0x09
#define HMC5883L_RA_ID_A            0x0A
#define HMC5883L_RA_ID_B            0x0B
#define HMC5883L_RA_ID_C            0x0C

//Configuration register A:
// CRA7 | CRA6 | CRA5 | CRA4 | CRA3 | CRA2 | CRA1 | CRA0
// rsv. |sample aver. |     output rate    | meas. config. 
#define HMC5883L_CRA_AVERAGE_BIT    6
#define HMC5883L_CRA_AVERAGE_LENGTH 2
#define HMC5883L_CRA_RATE_BIT       4
#define HMC5883L_CRA_RATE_LENGTH    3
#define HMC5883L_CRA_BIAS_BIT       1
#define HMC5883L_CRA_BIAS_LENGTH    2

#define HMC5883L_AVERAGING_1        0x00
#define HMC5883L_AVERAGING_2        0x01
#define HMC5883L_AVERAGING_4        0x02
#define HMC5883L_AVERAGING_8        0x03

#define HMC5883L_RATE_0P75          0x00
#define HMC5883L_RATE_1P5           0x01
#define HMC5883L_RATE_3             0x02
#define HMC5883L_RATE_7P5           0x03
#define HMC5883L_RATE_15            0x04
#define HMC5883L_RATE_30            0x05
#define HMC5883L_RATE_75            0x06

#define HMC5883L_BIAS_NORMAL        0x00
#define HMC5883L_BIAS_POSITIVE      0x01
#define HMC5883L_BIAS_NEGATIVE      0x02

//Configuration register B:
#define HMC5883L_CRB_GAIN_BIT       7
#define HMC5883L_CRB_GAIN_LENGTH    3

#define HMC5883L_GAIN_1370          0x00
#define HMC5883L_GAIN_1090          0x01
#define HMC5883L_GAIN_820           0x02
#define HMC5883L_GAIN_660           0x03
#define HMC5883L_GAIN_440           0x04
#define HMC5883L_GAIN_390           0x05
#define HMC5883L_GAIN_330           0x06
#define HMC5883L_GAIN_220           0x07

//Mode register:
#define HMC5883L_MODEREG_BIT        1
#define HMC5883L_MODEREG_LENGTH     2

#define HMC5883L_MODE_CONTINUOUS    0x00
#define HMC5883L_MODE_SINGLE        0x01
#define HMC5883L_MODE_IDLE          0x02

#define HMC5883L_STATUS_LOCK_BIT    1
#define HMC5883L_STATUS_READY_BIT   0

#endif /* _MPU6050_DEFINES_H_ */

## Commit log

2022-03-10 sch: add notes and circuits from 2022/03/10 lecture
    [PPSE_2021.sch, connectivity.sch, control.sch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]
2022-03-11 sch: add gps
    [PPSE_2021.sch, connectivity.sch, control.sch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]
2022-03-17 hw: migrate to kicad 6
    [PPSE_2021.kicad_pcb, PPSE_2021.kicad_sch, PPSE_2021.sch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]
2022-03-17 hw: add RP2040 footprint for hand soldering
    [PPSE_2021.kicad_pcb, PPSE_2021.kicad_sch, control.kicad_sch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]
2022-03-18 hw: fix crystal topology
    [PPSE_2021.kicad_sch, control.kicad_sch]
2022-03-23 hw: add flash, switching circuit and XOUT resistor, change GPS and general cleanup
    [PPSE_2021.kicad_sch, connectivity.kicad_sch, control.kicad_sch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]
2022-03-23 hw: add panel sensing and change GPS_EN to hierarchical pin
    [PPSE_2021.kicad_sch, connectivity.kicad_sch, sensing.kicad_sch]
2022-03-23 fw: added MPU9250
    [PPSE_2021.kicad_sch, sensing.kicad_sch]
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2022-03-24 fw: params fixed, except to elevation and azimuth + added calculations spreadsheet
    [NOAA_Solar_Calculations_day(1).ods]
2022-03-25 added ra_dec.ods doc
    [ra_dec.ods]
2022-03-25 hw: add limit switches, dual power input, actuation sheet, debug and expansion connectors and connect sheets
    [PPSE_2021.kicad_sch, actuation.kicad_sch, connectivity.kicad_sch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]
2022-03-25 fw: algo v0.90
    [NOAA_Solar_Calculations_day(1).ods]
2022-03-25 docs: moved noaa excel calcs to docs folder
    [NOAA_Solar_Calculations_day(1).ods]
2022-03-28 fw: added inline args
    [NOAA_Solar_Calculations_day(1).ods]
2022-03-28 hw: schematic updates
    [PPSE_2021.kicad_sch, actuation.kicad_sch, connectivity.kicad_sch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]
2022-03-29 hw: connect filtering capacitor near vdd pin
    [PPSE_2021.kicad_sch, actuation.kicad_sch, connectivity.kicad_sch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]
2022-03-29 hw: update schematic pt. 2
    add switching enable resistor, change usb inductor to ferrite bead, add OR gate and microstepping solder jumpers to motor driver, remove i2c and backup supply solder jumper from GPS, add ferrite bead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
    [PPSE_2021.kicad_sch, actuation.kicad_sch, connectivity.kicad_sch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]
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2022-03-30 hw: added MAN_NORD and TRCK_ON_OFF buttons and OLED Display
    [PPSE_2021.kicad_sch, actuation.kicad_sch, control.kicad_sch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]
2022-03-30 hw: set grid to 50 mils and missing labels
    [PPSE_2021.kicad_sch, actuation.kicad_sch, connectivity.kicad_sch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]
2022-03-30 hw: add stepper motor drivers
    [PPSE_2021.kicad_sch, actuation.kicad_sch, control.kicad_sch]
2022-03-31 hw: move inputs from control to sensing and outputs from control to actuation
    [PPSE_2021.kicad_sch, actuation.kicad_sch, control.kicad_sch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]
2022-03-31 hw: add TVS diode and comments
    [PPSE_2021.kicad_sch, power.kicad_sch]
2022-03-31 fw: discrete dirver for stepper
    [PPSE_2021.kicad_sch, actuation.kicad_sch, control.kicad_sch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]
2022-03-31 hw: add capacitor voltages, fix supply caps and other fixes
    add capacitor voltages, change polarized caps to normal, move switching capacitors, remove 5V power, fix switching ballast capacitor, remove switching feedback capacitor, switch sensing and actuation sub-sheets positions in main sheet, add labels to most nodes for pcb layout, connect GPS supply caps directly, remove biased transistor and ferrite bead from GPS enable MOSFET, remove unneeded pins from stepper motors connectors
    [PPSE_2021.kicad_sch, actuation.kicad_sch, connectivity.kicad_sch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]
2022-04-02 hw: add connectors and crystal footprints
    [PPSE_2021.kicad_sch, actuation.kicad_sch, control.kicad_sch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]
2022-04-03 hw: add footprints for resistors and capacitors and re-add specs documant that was deleted
    [PPSE_2021.kicad_sch, actuation.kicad_sch, connectivity.kicad_sch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]
2022-04-04 hw: update root pin and usb connector
    [PPSE_2021.kicad_sch, actuation.kicad_sch, control.kicad_sch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]
2022-04-04 hw: rgb led with NPN
    [PPSE_2021.kicad_sch, actuation.kicad_sch, control.kicad_sch]
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2022-04-04 hw: part of last checks and footprint assignments
    [PPSE_2021.kicad_sch, actuation.kicad_sch, connectivity.kicad_sch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]
2022-04-04 commit anonimo di thimas
    [PPSE_2021.kicad_sch, actuation.kicad_sch, connectivity.kicad_sch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]
2022-04-05 hw: add mounting holes
    [PPSE_2021.kicad_sch, actuation.kicad_sch, connectivity.kicad_sch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]
2022-04-05 hw: add PMDE footprint
    [PPSE_2021.kicad_sch, power.kicad_sch]
2022-04-05 hw: add last footprints
    [PPSE_2021.kicad_sch, connectivity.kicad_sch, power.kicad_sch]
2022-04-05 hw: first layout draft
    [PPSE_2021.kicad_pcb, PPSE_2021.kicad_sch, connectivity.kicad_sch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]
2022-04-07 hw: classroom changes
    [PPSE_2021.kicad_pcb, PPSE_2021.kicad_sch, control.kicad_sch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]
2022-04-07 hw: add fiducial to eeschema and change sw footprints
    [PPSE_2021.kicad_pcb, PPSE_2021.kicad_sch, control.kicad_sch]
2022-04-08 change mcu pins and optimize layout
    [PPSE_2021.kicad_pcb, PPSE_2021.kicad_sch, control.kicad_sch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]
2022-04-08 hw: power routing
    [PPSE_2021.kicad_pcb, PPSE_2021.kicad_sch, connectivity.kicad_sch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]
2022-04-08 hw: first round of routing
    [PPSE_2021.kicad_pcb, control.kicad_sch]
2022-04-09 hw: finalize routing (dbg uart missing)
    [PPSE_2021.kicad_pcb, control.kicad_sch]
2022-04-09 fw: partially fix makefile
    [SALMO.c]
2022-04-09 fw: fix building libraries with cmake
    [NOAA_Solar_Calculations_day(1).ods, ra_dec.ods]
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2022-04-11 hw: final changes
    [PPSE_2021.kicad_pcb, PPSE_2021.kicad_sch, connectivity.kicad_sch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]
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2022-04-11 fw: fix printf and algo warnings
    [SALMO.c, SALMO.h]
2022-04-12 hw: add gerber files
    [PPSE_2021-B_Cu.gbr, PPSE_2021-B_Mask.gbr, PPSE_2021-B_Silkscreen.gbr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]
2022-04-12 hw: small fixes to vias and silkscreen
    [PPSE_2021.kicad_pcb]
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2022-04-13 hw: add sensing resistance values
    [PPSE_2021.kicad_pcb, PPSE_2021.kicad_sch, control.kicad_sch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]
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2022-04-13 hw: final pcb check before submit
    [PPSE_2021-B_Cu.gbl, PPSE_2021-B_Cu.gbr, PPSE_2021-B_Mask.gbs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]
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2022-05-02 fix: HMC default address wrong define
    [HMC5883L.c]
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2022-05-05 fw: errata: add stepper
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2022-06-05 fw: add test with different locations. Tracking based on minutes is not working
    [SALMO.c]
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2022-06-20 chore: merged hw stuff with fw branch and fw: full home btn feature
    [PPSE_2021-B_Cu.gbl, PPSE_2021-B_Mask.gbs, PPSE_2021-B_Silkscreen.gbo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]
2022-06-20 fw: fix compilation errors
    [SALMO.c, SALMO.h]
2022-06-27 hw: add custom page layout
    [PPSE_2021.kicad_sch, actuation.kicad_sch, connectivity.kicad_sch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]
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2022-06-28 docs: update schematic pdf (SALMO Society logo is broken)
2022-06-28 docs: fix missing flowchart on readme
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2022-06-28 hw: changes for the simia
    [PPSE_2021.kicad_sch, connectivity.kicad_sch, control.kicad_sch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]
2022-06-29 hw: change some small notes
    [actuation.kicad_sch, control.kicad_sch, sensing.kicad_sch]
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2022-06-30 fw: add buzzer and startup tones
    [SALMO.c]
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2022-07-04 report: fix assembly and testing paragraphs and other changes
    other changes are increase linespread, add tocdepth limit, remove SALMO SOCIETY from title
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
